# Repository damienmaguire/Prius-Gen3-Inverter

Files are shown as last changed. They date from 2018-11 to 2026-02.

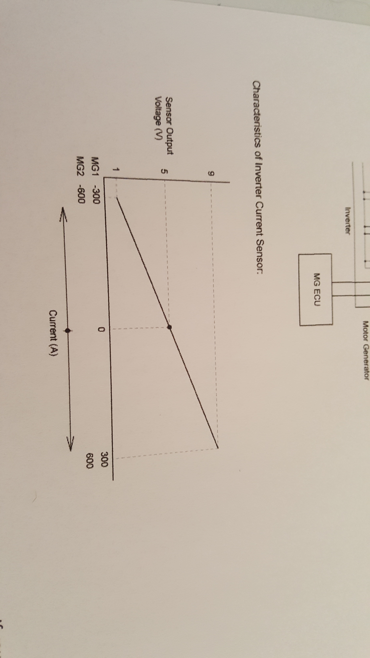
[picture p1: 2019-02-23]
current_sensor_curve.jpg

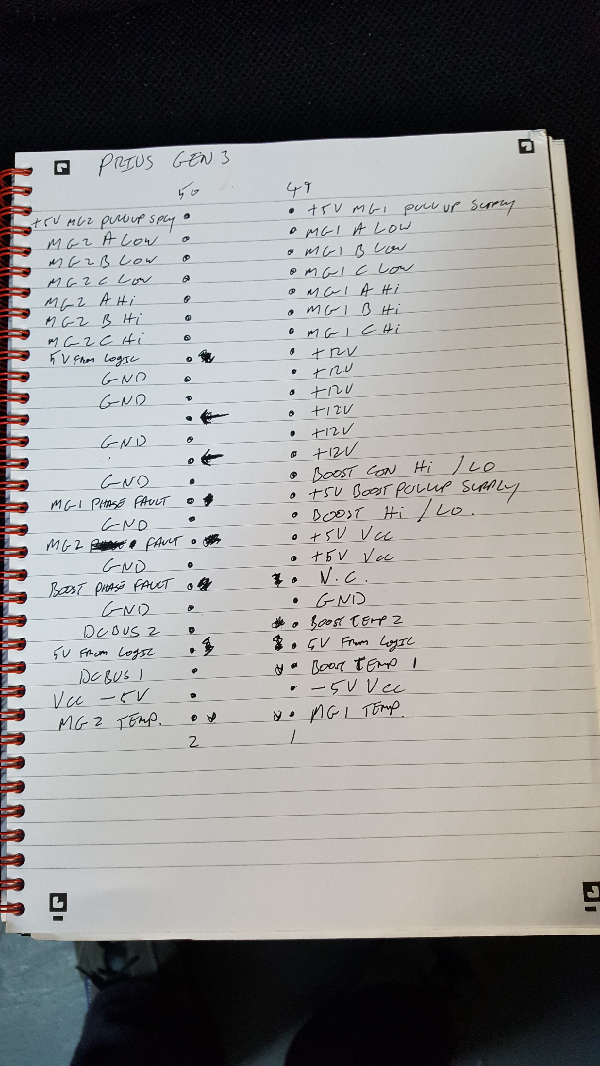
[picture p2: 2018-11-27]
IGBT_conn.jpg

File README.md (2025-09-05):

# Prius-Gen3-Inverter
Open source logic board to control the Toyota Prius Gen 3 Inverter

PCB Files in DesignSpark PCB 8.1 Format

Based on the Open Source Inverter system designed by Johannes Heubner.

27/11/18 Reverse engineering of the inverter continues. Now have all but two of the fifty pins of the igbt interface connector worked out.

01/12/18 Uploaded design for a simple breakout pcb to allow easier access to the 50 Way JST header used for connecting to the IGBT driver board.

01/03/19 Uploaded PDF of V1 logic board design for Gen 3 inverter / converter. Design on PCB commenced. Full design to be released soon.

06/03/19 : Initial release of V1 logic board design files and Gerbers. Changes likely before prototype ordering. BOM on the way.

12/03/19 : Released final design files. Now gone for pcb prototype build. Standby for fun:)

20/01/20 : Design files released for V2 board. Uses MG2 as inverter and MG1 and boost converter for battery charging. Based on the openinverter system. PCB files in DesignSpark PCB 9 format.

16/05/20 : Design files for new V1c board released.
<br>
Instalation video manual part one :
<br>
https://youtu.be/QE-zym8iIgM
<br>
Available on the webshop here :
<br>
https://www.evbmw.com/index.php/evbmw-webshop/toyota-built-and-tested-boards

28/06/20 : Road testing : https://youtu.be/Bs4mdTkqKXk

15/09/20 : New V1d Dual Motor version gerbers and schematics uploaded. This version features two STM32 MCUs to allow Both MG1 and MG2 in a Toyota hybrid transmission to be each controlled together or independently. Untested as of this date. Sources will be released in the future.

14/10/20 : Block 3 versions of V1c and V1d boards added. Changes :

V1c - Updated obsolete SG3204 charge pump -5v supply to LM2776.

V1d - Changed pullups / pulldowns on the MG1 MCU to avoid it being detected as a Tesla M3 board by the firmware.

V1d - Updated obsolete SG3204 charge pump -5v supply to LM2776.

Dual motor board working :

https://www.youtube.com/watch?v=aW6XFF3Rs8Q

18/01/2021 :(180Jacob) Small board layout of V1d uploaded. Note at time of writing, the low side output drivers are out of stock at JLC so I will change the BOM once an alternative is chosen.

05/09/25 : Added Ampseal adapter board gerber files

20/01/21 : Added Sync serial data captures between new VCU and bench rig (ct200h) and various prius and yaris bare logic boards.

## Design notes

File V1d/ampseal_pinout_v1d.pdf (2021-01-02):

## PRIUS GEN 3 V1d LOGIC BOARD AMPSEAL 35 PINOUT

PIN | FUNCTION
1 | 12V SUPPLY POSITIVE
2 | GROUND
3 | FORWARD DIRECTION SIGNAL
4 | REVERSE DIRECTION SIGNAL
5 | START SIGNAL
6 | BRAKE DIGITAL SIGNAL
7 | CRUISE CONTROL SIGNAL
8 | +5V OUT
9 | ACCELERATOR CHAN 1 INPUT
10 | ACCELERATOR CHAN 2 INPUT
11 | GROUND
12 | MG1 RESOLVER EXC
13 | MG1 STATOR TEMP SENSOR B
14 | +5V OUT
15 | MG2 ENCODER CHAN A
16 | MG2 ENCODER CHAN B
17 | GROUND
18 | RESOLVER SIN
19 | RESOLVER COS
20 | MG2 RESOLVER EXC
21 | GROUND
22 | MG2 STATOR TEMP SENSOR A

23 | MG2 STATOR TEMP SENSOR B
24 | MAIN HV CONTACTOR
25 | HV PRECHARGE RELAY
26 | CHARGER AC INPUT RELAY
27 | CHARGER HV DC REQUEST
28 | CHARGER AC PRECHARGE RELAY
29 | MG1 STATOR TEMP A
30 | EVSE PROXIMITY SIGNAL
31 | EVSE CONTROL PILOT SIGNAL
32 | CHARGER CAN HIGH
33 | CHARGER CAN LOW
34 | MG1 ENCODER CHAN A
35 | MG1 ENCODER CHAN B

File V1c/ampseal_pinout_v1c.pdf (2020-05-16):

## PRIUS GEN 3 V1c LOGIC BOARD AMPSEAL 35 PINOUT

PIN | FUNCTION
1 | 12V SUPPLY POSITIVE
2 | GROUND
3 | FORWARD DIRECTION SIGNAL
4 | REVERSE DIRECTION SIGNAL
5 | START SIGNAL
6 | BRAKE DIGITAL SIGNAL
7 | CRUISE CONTROL SIGNAL
8 | +5V OUT
9 | ACCELERATOR CHAN 1 INPUT
10 | ACCELERATOR CHAN 2 INPUT
11 | GROUND
12 | INVERTER CAN HIGH
13 | INVERTER CAN LOW
14 | +5V OUT
15 | ENCODER CHAN A
16 | ENCODER CHAN B
17 | GROUND
18 | RESOLVER SIN
19 | RESOLVER COS
20 | RESOLVER EXC
21 | GROUND
22 | MOTOR TEMP SENSOR A

23 | MOTOR TEMP SENSOR B
24 | MAIN HV CONTACTOR
25 | HV PRECHARGE RELAY
26 | CHARGER AC INPUT RELAY
27 | CHARGER HV DC REQUEST
28 | CHARGER AC PRECHARGE RELAY
29 | GROUND
30 | EVSE PROXIMITY SIGNAL
31 | EVSE CONTROL PILOT SIGNAL
32 | CHARGER CAN HIGH
33 | CHARGER CAN LOW
34 | NOT USED
35 | NOT USED

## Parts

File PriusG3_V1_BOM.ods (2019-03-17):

TOYOTA PRIUS GEN 3 INVERTER LOGIC BOARD V1 BOM
Ref Name | Qty | Component | Value | Manufacturer | MPN | RS Part Number | Mouser Part Number | Description
CONN1 | 1 | G3_Main_Conn |  | Tyco |  | See Notes(1) | See Notes(1) | Not available. Must be harvested from OEM logic PCB.
CONN8,9 | 2 | 2PinJSTCPT |  | JST (JAPAN SOLDERLESS TERMINALS) | SM02B-CPTK-1A-TB | 123-8260 |  | Wire-To-Board Connector, 2 mm, 2 Contacts, Header, CPT Series, Crimp, 1 Rows
CONN7,12,13,14,15,16 | 6 | 2SIL |  | AMPHENOL FCI | 77311-401-36LF | 771-0189 |  | Board-To-Board Connector, 2.54 mm, 36 Contacts, Header, BergStik 77311 Series, Through Hole, 1 Rows
CONN11 | 1 | 6DSIL |  | Wurth Elektronik | 61300421121 | 828-1513 |  | 2.54mm Pitch, 4 Way, 2 Row, Straight Pin Header, Through Hole
CONN3 | 1 | 8PinJSTCPT |  | JST (JAPAN SOLDERLESS TERMINALS) | SM08B-CPTK-1A-TBL |  | 306-SM08B-CPTK-1ATBL | Automotive Connectors SIDE ENTRY CPT HDR 2.0MM PITCH
C44 | 1 | 25PX680MEFC10X12.5 | 680uF | Rubycon | 25PX680MEFC10X12.5 | 711-1141 |  | RUBYCON - 25PX680MEFC10X12.5 - CAP, 680F, 25V, 20%
C104,109 | 2 | 25ZLG47MEFC6.3X7 | 47uF | Rubycon | 25ZLG47MEFC6.3X7 | 7259004 |  | Capacitor Al 105deg 47uF 25V 6.3x7 Rubycon Aluminium Electrolytic Capacitor 47uF 25 V dc 6.3mm
J2,3 | 2 | 75867-101LF |  | FCI | 75867-101LF | 6737635 |  | 2.54mm Pitch 10 Way 2 Row Shrouded Right Angle PCB Header, Through Hole
L1 | 1 | 7447709470 |  | Wurth Elektronik | 7447709470 | 789-6805 |  | SMD-Shielded Power Inductors WE-PD
IC12 | 1 | AT90S4433A | ATMEGA328P-AU | Microchip | ATMEGA328P-AU | 131-0271 |  | MICROCONTROLLER4 Kbytes FLASH128 bytes SRAM256 bytes EEPROMUART6-channel 10 bit ADC
CONN4,5 | 2 | BM08B-CPTK-1A-TB |  | JST (JAPAN SOLDERLESS TERMINALS) | BM08B-CPTK-1A-TB | 1238259 |  | Header Top 8 Double CPT
CONN2 | 1 | BM50B-SHLDS-G-TFT |  | JST (JAPAN SOLDERLESS TERMINALS) | BM50B-SHLDS-G-TFT | See Notes(2) | See Notes(2) | Top Entry disconnectable, crimp style Shrouded Header, 50 positions
C41,23,24,106,43,65,71,107,72,84,97,98,99,100,111,113,114,9,52,58 | 20 | C-USC0805 | 0.1uF | MURATA | GRM219R71C104KA01D |  | 81-GRM40X104K16D | Murata 0805 GRM 100nF Ceramic Multilayer Capacitor, 16 V dc X7R Dielectric ±10% SMD
C18,19,20,33,34,69,70,85,86,89 | 10 | C-USC0805 | 1nF | MULTICOMP | MCSH21B102K160CT | 1856432 |  | SMD Multilayer Ceramic Capacitor, 0805 [2012 Metric], 1000 pF, 16 V, ± 10%, X7R, MCSH Series
C21,22,25,26,28,29,30,31,32,45,40,77,82,83,90,91,92,93,94,95,96,101,102,112,115,6,7,14,15,53,62,11,16,64,66 | 35 | C-USC0805 | 1uF | KEMET | C0805C105K4RACTU | 9227792 |  | Kemet 0805 1μF Ceramic Multilayer Capacitor, 16V dc X7R Dielectric ±10% SMD
C46,55,56 | 3 | C-USC0805 | 10nF | Wurth Elektronik | 885012207039 | 181-4070 |  | SMD Multilayer Ceramic Capacitor, 0805 [2012 Metric], 0.01 µF, 16 V, ± 10%, X7R,
C36,37,38,49,50,73,74,75,80,81 | 10 | C-USC0805 | 22n | Avx | 08051C223KAT2A | 136-4708 |  | 22nF Multilayer Ceramic Capacitor MLCC
C1,2,4,8 | 4 | C-USC0805 | 27pF | MULTICOMP | MC0805N270J500CT | 1759196 |  | SMD Multilayer Ceramic Capacitor, 0805 [2012 Metric], 27 pF, 50 V, ± 5%, C0G / NP0, MC Series
C105,108 | 2 | C-USC0805 | 47nF | YAGEO (PHYCOMP) | CC0805KRX7R9BB473 | 718683 |  | SMD Multilayer Ceramic Capacitor, 0805 [2012 Metric], 0.047 µF, 50 V, ± 10%, X7R, CC Series
C39,76 | 2 | C-USC0805 | 330n | Avx | 08055C334KAT2A | 144-1441 |  | 330nF Multilayer Ceramic Capacitor MLCC 50V dc
C3,27,35,68,87,88,47,48,78,79 | 10 | Cap_el | 100uF | Nichicon | UPS1E101MED | 519-4059 |  | 100μF 25V dc Aluminium Electrolytic Capacitor, Through Hole 6.3 (Dia.) x 11mm +105°C 6.3mm 2.5mm
IC5 | 1 | CD74HC30M |  | Texas Instruments | CD74HC30M | 526824 |  | CD74HC30M, Logic Gate 8 Input NAND, HC, 5.2mA 2 to 6V 14-Pin SOIC
L4,5 | 2 | CLF7045T-150M |  | TDK | CLF7045T-150M | 7923997P |  | TDK CLF7045T Series Shielded Wire-wound SMD Inductor with a Ferrite Core, 15 uH +/-20% 2.3A Idc
X2,4 | 2 | CRYSTALTC26HM | 32.768kHz | RALTRON | R26-32.768- 12.5 | 1652573 |  | Crystal, 32.768 kHz, Cylinder Radial, 6.2mm x 2mm Dia, 12.5 pF, 20 ppm, R26 Series
C12,13,59,63 | 4 | C_0805 | 10pF | Wurth Elektronik | 885012007010 |  | 710-885012007010 | SMD Multilayer Ceramic Capacitor, 0805 [2012 Metric], 10 pF, 16 V, ± 5%, C0G / NP0
C5,17,60,61,10,67 | 6 | C_0805 | 10uF | MURATA | GRM21BR61E106KA73L | 790-0673 |  | SMD Multilayer Ceramic Capacitor, 0805 [2012 Metric], 10 µF, 25 V, ± 10%, X5R, GRM Series
LD1,2 | 2 | LD1117SOT223 | LD1117-3.3 | STMICROELECTRONICS | LD1117S33CTR | 686-9388 |  | Fixed LDO Voltage Regulator, 4.75V to 15V, 1.1V Dropout, 3.3Vout, 950mAout, SOT-223-4
LED2,1,3,4,5 | 5 | LED0805 |  | MULTICOMP | MCL-S270GC | 1581242 |  | LED, Green, SMD, 1.25mm x 1.4mm, 20 mA, 2.1 V, 570 nm
X1,3 | 2 | LFXTAL011301 | 8.00MHz | IQD | LFXTAL011301 | 4789656 |  | Crystal SMD 8.000MHz HC49S-SMD Crystal 8MHz, 30ppm, 2-Pin HC-49-4H-SMX
IC2,17 | 2 |  |  | Winslow | W30508TRC | 813-115 |  | 2.54mm Pitch Vertical 8 Way, Through Hole Turned Pin Open Frame IC Dip Socket
IC2,17 | 2 | LM386N |  | Texas Instruments | LM386N | 124-4528 |  | Audio Amplifiers Lo Vltg Audio PWR Amp
IC8 | 1 | LM2596S-5.0_NOPB |  | Texas Instruments | LM2596S-5.0/NOPB | 5333692 |  | SIMPLE SWITCHER 4.5V to 40V, 3A Low Component Count Step-Down Regulator
IC4,18 | 2 | LM2901DT |  | STMicroelectronics | LM2901DT | 7140745 |  | LM2901DT, Quad Comparator Open Collector 1.3s 12 V, 15 V, 18 V, 24 V, 28 V, 3 V, 5 V, 9 V 14-Pin SO
L2,3 | 2 | L_PM0603 | 10uH | TDK | MLZ1608M100WT |  | 810-MLZ1608M100WT000 | Surface Mount High Frequency Inductor, MLZ Series, 10 µH, 250 mA, 0603 [1608 Metric], Multilayer
IC3 | 1 | MAX889RESA+ |  | Maxim Integrated | MAX889RESA+ | 7861300P |  | Maxim MAX889RESA+, Charge Pump Inverting 200mA 0.62 MHz, -2.5 -5.5 V, 8-Pin, SOIC
D1,2,3,4 | 4 | MBRS540T3G |  | ON Semiconductor | MBRS540T3G | 1250012 |  | Diode Schottky 40V 5A SMC ON Semiconductor MBRS540T3G Schottky Diode, 5A, 40V, 2-Pin SMC
C51 | 1 | MCGPR10V227M6.3X11 | 220uF | MULTICOMP | MCGPR10V227M6.3X11 | 711-0808 |  | MULTICOMP - MCGPR10V227M6.3X11 - CAP, 220F, 10V, 20%
IC7,11 | 2 | MCP602-I_SN |  | Microchip | MCP602-I/SN | 3792588 |  | Dual lowpower op-amp,MCP602-I/SN SO8
C54,102 | 2 | MCRH35V477M10X21 | 470uF | MULTICOMP | MCRH35V477M10X21 | 711-1292 |  | MULTICOMP - MCRH35V477M10X21 - CAP, 470F, 35V, 20%
IC6,19 | 2 | MIC2171WU-TR |  | Micrel | MIC2171WU-TR | 998-MIC2171WUTR |  | Switching Voltage Regulators 2.5A 100kHz Switching Regulator
J1 | 1 | ML6 |  | HARTING | 9185067324 | 740-7105 |  | Harting SEK Series, 2.54mm Pitch 6 Way 2 Row Straight PCB Header
TR1,2,3,4,5,6,7,8,9,10,11,12,13,14,15 | 15 | MMBT3904 |  | Fairchild Semiconductor | MMBT3904 | 7390303 |  | NPN 40V 0.2A SOT23 Fairchild MMBT3904 NPN Bipolar Transistor, 0.2 A, 40 V, 3-Pin SOT-23
IC13,14 | 2 | NCV8401ADTRKG |  | ON Semiconductor | NCV8401ADTRKG | 8079877 |  | ON Semiconductor NCV8401ADTRKG Load Switch IC 3-Pin, DPAK
R125,126,53 | 3 | R-US_R0805 | 0R | RS Pro | 717-1578 | 717-1578 |  | 0R 0805 Thick Film Surface Mount Fixed Resistor ±5% 0.125W
R8,6,38,39,40,41,42,43,58,89,98,99,100,101,102,103,129,130,153,154,164,165,178,179,180,181,152,182,183,184,185,186,187,188,189,190,191,192,195,196 | 40 | R-US_R0805 | 1k | MULTICOMP | MC01W080551K | 9333711 |  | SMD Chip Resistor, Thick Film, 1 kohm, 150 V, 0805 [2012 Metric], 100 mW, ± 5%, MC Series
R52,166,174,176 | 4 | R-US_R0805 | 1K2 | RS Pro | 713-6941 | 713-6941 |  | 1.2kΩ 0805 Thick Film Surface Mount Fixed Resistor ±5% 0.125W
R24,26,28,32,33,141,143,144,146,147 | 10 | R-US_R0805 | 1K5 | Panasonic | ERJ6RBD1501V | 2380317 |  | SMD Chip Resistor, Thick Film, 1.5 kohm, 150 V, 0805 [2012 Metric], 100 mW, ± 0.5%, ERJ6E Series
R57,65,118,167,173,175 | 6 | R-US_R0805 | 2K2 | RS Pro | 804-6455 | 804-6455 |  | 1.5kΩ 0805 Thick Film Surface Mount Fixed Resistor ±1% 0.125W
R3,7,17,66,67,104,105,119,120,135 | 10 | R-US_R0805 | 3K3 | Panasonic | ERJ6RBD3301V | 2380370 |  | SMD Chip Resistor, Thick Film, 3.3 kohm, 150 V, 0805 [2012 Metric], 100 mW, ± 0.5%, ERJ6E Series
R48,110 | 2 | R-US_R0805 | 3K16 | RS Pro | 717-2644 | 717-2644 |  | 3.16kΩ 0805 Thick Film Surface Mount Fixed Resistor ±1% 0.125W
R47,23,25,27,31,34,109,142,145,148,149,150,11,90 | 14 | R-US_R0805 | 4K7 | Panasonic | ERJ6RBD4701V | 2380397 |  | SMD Chip Resistor, Thick Film, 4.7 kohm, 150 V, 0805 [2012 Metric], 100 mW, ± 0.5%, ERJ6E Series
R160,162 | 2 | R-US_R0805 | 9K1 | RS Pro | 804-6512 | 804-6512 |  | 9.1kΩ 0805 Thick Film Surface Mount Fixed Resistor ±1% 0.125W
R2,4,9,10,12,14,15,46,51,1,18,19,20,21,29,30,36,37,22,55,59,60,13,91,92,93,94,95,96,108,113,114,115,122,123,124,127,128,136,137,138,139,140,151,156,168,169,,170,171,172,177 | 51 | R-US_R0805 | 10k | BOURNS | CRT0805-FZ-1002ELF | 2008317 |  | SMD Chip Resistor, Thin Film, 10 kohm, 100 V, 0805 [2012 Metric], 100 mW, ± 1%, CRT Series
R68,121 | 2 | R-US_R0805 | 10R | RS Pro | 713-6771 | 713-6771 |  | 10R 0805 Thick Film Surface Mount Fixed Resistor ±5% 0.125W
R35,73 | 2 | R-US_R0805 | 56K | RS Pro | 804-6580 | 804-6580 |  | 56kΩ 0805 Thick Film Surface Mount Fixed Resistor ±1% 0.125W
R69,70,116,117 | 4 | R-US_R0805 | 60R4 | TE CONNECTIVITY | RN73C2A60R4BTDF | 2688288RL |  | SMD Chip Resistor, Precision, 60.4 ohm, 100 V, 0805 [2012 Metric], 100 mW, ± 0.1%
R44,49,106,111 | 4 | R-US_R0805 | 62K | RS Pro | 804-6584 | 804-6584 |  | 62kΩ 0805 Thick Film Surface Mount Fixed Resistor ±1% 0.125W
R74,75,76,77,78,79,193,194,82,83,84,85,86,87 | 14 | R-US_R0805 | 91R | RS Pro | 804-6363 | 804-6363 |  | 91Ω 0805 Thick Film Surface Mount Fixed Resistor ±1% 0.125W
R45,50,107,112,157,159 | 6 | R-US_R0805 | 100K | MULTICOMP | MC01W08055100K | 9333738 |  | SMD Chip Resistor, 100 kohm, 150 V, 0805 [2012 Metric], 100 mW, ± 5%, MC Series
R61,62,63,64,131,132,133,134 | 8 | R-US_R0805 | 220R | RS Pro | 713-6884 | 713-6884 |  | 220Ω 0805 Thick Film Surface Mount Fixed Resistor ±5% 0.125W
R158 | 1 | R-US_R0805 | 300K | RS Pro | 804-6644 | 804-6644 |  | 300kΩ 0805 Thick Film Surface Mount Fixed Resistor ±1% 0.125W
R5,88,155,163 | 4 | R-US_R0805 | 470R | RS Pro | 804-6417 | 804-6417 |  | 470Ω 0805 Thick Film Surface Mount Fixed Resistor ±1% 0.125W
R56,71,72 | 3 | R-US_R0805 | 560R | VISHAY | CRCW0805560RFKEA | 1469945 |  | SMD Chip Resistor, Thick Film, 560 ohm, 150 V, 0805 [2012 Metric], 125 mW, ± 1%
R161 | 1 | R-US_R0805 | 820R | RS Pro | 713-6932 | 713-6932 |  | 820Ω 0805 Thick Film Surface Mount Fixed Resistor ±5% 0.125W
X5 | 1 | RESONATORMU | 16MHz | MURATA | CSTCE16M0V53A-R0 | 721-4818 |  | Ceramic Resonator, 16MHz Fundamental 15pF, 3-Pin Cap Chip
IC9,16 | 2 | SN65HVD234 | SN65HVD234 | TEXAS INSTRUMENTS | SN65HVD234D | 1212363 |  | CAN Bus, Transceiver, CAN, 1, 1, 3 V, 3.6 V, SOIC
IC1,10 | 2 | STM32F103 | STM32F103RBT6 | STMICROELECTRONICS | STM32F103RBT6 | 1447640 |  | ARM Microcontroller, Motor Control, ARM Cortex-M3, 32bit, 72 MHz, 128 KB, 20 KB, 64 Pins
CONN6,10 | 2 | T821120A1S100CEU |  | AMPHENOL | T821120A1S100CEU | 8323499 |  | 2.54mm Pitch 20 Way 2 Row Shrouded Straight PCB Header, Through Hole, Solder Termination
IC20 | 1 | ULN2003ADR |  | Texas Instruments | ULN2003ADR | 6658699P |  | Texas Instruments ULN2003ADR, 7-element NPN Darlington Transistor Array, 0.5 A 50 V, 16-Pin SOIC
BOM Notes : 1) Conn 1 is a Tyco part but on their restricted list so must be removed from OEM board. (2) Conn 2 only available from ChipOneStop In Japan : https://www.chip1stop.com/USA/en/product/detail?mpn=BM50B-SHLDS-G-TFT%28LF%29%28SN%29&partId=JST1-0008157 (3) IC2,IC17 to be socketed.

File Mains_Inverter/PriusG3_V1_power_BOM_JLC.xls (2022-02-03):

Comment | Designator | Package | LCSC Part #
1N4148WS | D1,D4,D3,D7 | SOD-323F | C2128
ATMEGA328P-AU | IC10 | TQFP-32_7.0x7.0x0.8P | C14877
0.1uF | C18,C6,C24,C31,C30,C38,C5,C11,C9,C10,C21 | 0805_C | C49678
1nF | C37,C34,C35,C36,C26,C25 | 0805_C | C46653
1uF | C28,C1,C2,C13 | 0805_C | C28323
10nF | C23,C3,C27 | 0805_C | C1710
4.7uF | C33,C29,C32 | 1206_C | C29823
1.5NF | C7 | 0805_C | C1717
10uF | C22,C20 | 0805_C | C15850
DB107S | BR1,BR2,BR3 | DBS | C5377
RED LED | LED1,LED2 | LED_0805 | C84256
MC34063ABD-TR | IC5 | SOP-8_3.9x4.9x1.27P | C81155
MCP2515-I/SO | IC9 | SOIC-18_7.5x11.5x1.27P | C12368
MMBT3904 | TR3,TR6,TR4,TR7,TR5,TR8,TR10,TR9,TR1,TR2,TR11 | SOT-23-3 | C20526
MP2359DJ-LF-Z | IC6 | TSOT-23-6 | C14259
MWSA0402S-3R3MT | L1 | SMD-PIND-4.2x4.4x2.0_0.8x2.0 | C408336
NCV8402ASTT1G | IC1,IC2,IC3,IC4 | SOT-223 | C77755
0Ω | R1,R33 | 0805_R | C17477
1KΩ | R31,R36,R32,R27,R75,R63,R11,R41,R44,R45,R43,R46,R74,R76,R8,R29,R30 | 0805_R | C17513
1.5KΩ | R6,R10 | 0805_R | C4310
2.2KΩ | R26 | 0805_R | C17520
2.4KΩ | R28 | 0805_R | C17526
2.7KΩ | R5 | 0805_R | C17530
3.3KΩ | R61,R68 | 0805_R | C17520
3.6KΩ | R48,R57 | 0805_R | C17526
4.7KΩ | R35,R34,R37,R38 | 0805_R | C17530
6.2KΩ | R47,R56 | 0805_R | C17767
8.2KΩ | R13 | 0805_R | C17828
10KΩ | R15,R17,R18,R14,R19,R12,R62,R40,R9,R69,R16,R2,R55 | 0805_R | C17414
22KΩ | R7 | 0805_R | C17560
43KΩ | R21 | 0805_R | C17695
47kΩ | R25 | 0805_R | C17713
0.22Ω | R23 | 0805_R | C36234
100KΩ | R60,R58,R24 | 0805_R | C17407
100Ω | R67,R66,R49,R52,R50,R53,R51,R54,R64,R71,R65,R72,R70,R73 | 0805_R | C17408
120Ω | R20 | 0805_R | C17437
180Ω | R22 | 0805_R | C25270
300KΩ | R59 | 0805_R | C17616
330Ω | R3 | 0805_R | C17630
560Ω | R39 | 0805_R | C28636
680Ω | R4 | 0805_R | C17798
SGM3204 | PS1 | SOT-23-6L | C194031
SS54 | D2,D5,D6 | SMA,DO-214AC | C22452
220uH | L2 | SMD-PIND-12.5x12.5x5_2.9x5.4 | C169402
100uF 6.3V | C12,C14,C16,C19,C17 | CASE-B_3528 | C16133
TJA1050T | IC7 | SOIC-8_3.9x4.9x1.27P | C6952
100uf 25v | C4 | SMD-ECAP-6.3x7.7 | C176675
470uF 25V | C8 | SMD-ECAP-10x10 | C249931
330uF 35V | C15 | SMD-ECAP-10x10 | C134522
16MHZ | X1,X2,X3 | SMD-3225_4P | C13738
3V3 REG | LD1 | SOT-23-3L | C5446

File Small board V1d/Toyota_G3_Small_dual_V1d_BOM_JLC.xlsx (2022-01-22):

Comment | Designator | Footprint | JLCPCB Part #
1N4148WS | D1,D4,D3,D8,D7 | SOD-123 | C81598
AMS1117-3.3 | IC15 | SOT-223 | C6186
ATMEGA328P-AU | IC14 | TQFP-32_7.0x7.0x0.8P | C14877
0.1uF | C44,C54,C64,C88,C89,C65,C55,C13,C28,C51,C73 | 0805_C | C49678
1nF | C87,C67,C68,C33,C32,C69,C84,C85,C47,C46 | 0805_C | C46653
1uF | C12,C14,C6,C8,C10,C5,C9,C11,C4,C56,C1,C2,C90,C21,C31,C59,C53,C62,C60,C25,C71,C72,C76,C77,C83,C82,C61 | 0805_C | C28323
10nF | C50,C57,C48,C70 | 0805_C | C1710
22n | C43,C39,C35,C29,C23,C24,C74,C75,C78,C79,C80,C36 | 0805_C | C1729
22pF | C49,C45,C17,C16 | 0805_C | C1804
2.2uF | C91,C66 | 0805_C | C49217
1n5 | C15 | 0805_C | C1717
10uF | C41,C52,C20,C3,C18,C81,C58,C86,C92 | 0805_C | C15850
RED LED | LED1,LED2,LED4 | LED_0805 | C84256
10uH | L1,L4 | 0603 | C1035
MH2029-300Y | L5,L6 | 0805 | C1046
MC34063ABD-TR | IC7 | SOP-8_3.9x4.9x1.27P | C81155
MCP2515-I/SO | IC12 | SOIC-18_7.5x11.5x1.27P | C12368
MMBT3904 | TR1,TR4,TR2,TR5,TR3,TR6,TR15,TR14,Q1,TR7,TR8,TR11,TR9,TR12,TR10,TR13 | SOT-23-3 | C20526
NCV8402ASTT1G | IC3,IC1,IC6,IC4,IC2 | SOT-223 | C77755
0Ω | R64,R1,R135,R137,R59,R82 | 0805_R | C17477
1KΩ | R63,R61,R67,R78,R99,R77,R98,R60,R44,R43,R117,R104,R22,R28,R9,R25,R70,R73,R71,R72,R74,R116,R118,R47,R8,R111,R51,R54,R52,R55,R53,R56,R129,R130,R131,R132,R133,R127,R134,R83,R84,R119 | 0805_R | C17513
1.2KΩ | R114,R138 | 0805_R | C17379
1.5KΩ | R14,R16,R20,R11,R18,R6 | 0805_R | C4310
2.2KΩ | R115,R136,R139 | 0805_R | C17520
2.4KΩ | R39 | 0805_R | C17526
2.7KΩ | R5 | 0805_R | C17530
3.3KΩ | R57,R50,R96,R108,R120,R122 | 0805_R | C26010
3.6KΩ | R92,R80,R45,R46 | 0805_R | C18359
4.7KΩ | R17,R12,R19,R15,R21,R68,R121 | 0805_R | C17673
6.2KΩ | R79,R91,R42,R41 | 0805_R | C17767
8.2KΩ | R140,R141 | 0805_R
10KΩ | R75,R58,R76,R49,R48,R24,R27,R23,R26,R97,R69,R10,R109,R2,R13,R124,R125,R126,R40 | 0805_R | C17414
10Ω | R37,R123 | 0805_R | C17734
22KΩ | R7,R142 | 0805_R | C17560
47kΩ | R38 | 0805_R | C17713
0.22Ω | R36 | 0805_R | C36234
100KΩ | R95,R93,R143 | 0805_R | C17407
100Ω | R107,R106,R81,R87,R85,R88,R86,R89,R101,R100,R105,R112,R110,R113 | 0805_R | C17408
120Ω | R31 | 0805_R | C17437
180Ω | R35 | 0805_R | C25270
220Ω | R29,R30,R33,R34 | 0805_R | C17557
300KΩ | R94 | 0805_R | C17616
330Ω | R3 | 0805_R | C17630
560Ω | R66 | 0805_R | C28636
680Ω | R62,R4,R128 | 0805_R | C17798
LM2776DBVR | IC17 | SOT-23-6L | C69527
SN74LVC1G00DCKR | IC16 | SOT-353 | C8185
SS54 | D5,D2,D6 | SMA,DO-214AC | C22452
STM32F103RBT6 | IC13,IC9 | LQFP-64_10.0x10.0x0.5P | C8735
220uH | L3 | SMD-PIND-12.5x12.5x5_2.9x5.4 | C169391
68uH | L2 | SMD-PIND-12.5x12.5x8_2.9x5.4 | C169377
100uF 6.3V | C63,C30,C34,C38,C40,C19,C22 | CASE-B_3528 | C16133
TDA2822 | IC10 | SOP-8_3.9x4.9x1.27P | C73296
TJA1050T | IC11 | SOIC-8_3.9x4.9x1.27P | C6952
100uf 25v | C27 | SMD-ECAP-6.3x7.7 | C176664
330uF 25V | C7 | SMD-ECAP-8x10 | C134842
330uF 35V | C37 | SMD-ECAP-10x10 | C311621
8MHz | X1,X3 | SMD-5032_2P | C115962
16MHZ | X2,X4 | SMD-3225_4P | C13738
XL1509-5.0E1 | IC5 | SOP-8_3.9x4.9x1.27P | C61063
SI2301CDS-T1-GE3 | Q2 | SOT-23 | C10487

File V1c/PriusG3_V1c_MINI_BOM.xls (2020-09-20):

Comment | Designator | Package | LCSC Part # | Element14 Part # | chip1stop.com
Coolant Temp Sensor | CONN1 | SM02B-CPTK-1A-TB | C595136 | 2708677
MG2 Current Sense | CONN2 | BM08B-CPTK-1A-TB | C594390 | 2708676
DC/DC On/Off Jumper | CONN3 | 2SIL
ACS758LCB-100U output current sensor (Alegro) | CONN4 | 3WAY_SIL
DCDC Output Volt CON | CONN5 | 2SIL
IGBT Board Interface | CONN6 | BM50B-SHLDS-G-TFT | N.A. | N.A. | C1S404000081575
MG1 Current Sense | CONN7 | BM08B-CPTK-1A-TB | C594390 | 2708676
External HVIL | CONN8 | SM02B-CPTK-1A-TB | C595136 | 2708677
FTDI Header for CHG MCU | CONN9 | 6SIL
DC/DC Converter Interface | CONN10 | SM08B-CPTK-1A-TB | C264977 | 2708679
Main Input Connector 34 Way IDC to input PCB | J1 | 75869-106LF | N.A. | 1103954
ESP WiFi Module | J2 | 75867-101LF | C598980 | 1103956
ICSP Header for CHG MCU | J3 | Pin Header Strip (2 singles)
Tag Connect JTAG | J3 | TC2050-IDC-NL | N.A. | N.A
Single Wire Programming Port STM32 | SWPR001 | Pin Header Strip

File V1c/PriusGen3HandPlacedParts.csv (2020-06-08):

Ref Name | Qty | Component | Value | Manufacturer | MPN | RS Part Number | Mouser Part Number | LCSC Part Number | Description
CONN1; CONN8 | 2 | 2PinJSTCPT |  | JST | SM02B-CPTK-1A-TB | 123-8260 |  |  | Wire-To-Board Connector 2mm 2-Contacts Header CPT Series Crimp 1 Rows
CONN2; CONN7 | 2 | BM08B-CPTK-1A-TB |  | JST | BM08B-CPTK-1A-TB | 1238259 |  |  | Header Top 8 Double CPT
CONN3; CONN5 | 2 | PIN HEADER |  |  |  |  |  |  | 2X1X2.5MM Jumpers for DC/DC operation
CONN4; SWPR001 | 2 | PIN HEADER |  |  |  |  |  |  | 3x1x2.5MM
CONN6 | 1 | BM50B-SHLDS-G-TFT |  | JST | BM50B-SHLDS-G-TFT | See Notes | See Notes | See Notes | Top Entry disconnectable crimp style Shrouded Header 50 positions
CONN9 | 1 | PIN HEADER |  |  |  |  |  |  | 1X6X2.5
CONN10 | 1 | 8PinJSTCPT |  | JST | SM08B-CPTK-1A-TBL |  | 306-SM08B-CPTK-1ATBL |  | Automotive Connectors SIDE ENTRY CPT HDR 2.0MM PITCH
J1 | 1 | 90º LOCKING IDC |  | 3M | N3431-5302RB | 5429153 | 517-N3431-5302RB |  | 3M 3000 Series; 2.54mm Pitch 34 Way 2 Row Right Angle PCB Header; Solder Term; 2A
J2 | 1 | 90º PIN HEADER |  | 3M | N2510-5002RB | 5428908 | 517-N2510-5002RB |  | Header; High Temperature; PCB Plug; 10 Cont; Solder Tail; Thru-Hole; 2500 Series; 2A
J3 | 1 | ML6 |  | HARTING | 9185067324 | 740-7105 |  |  | Harting SEK Series 2.54mm Pitch 6 Way 2 Row Straight PCB Header
NOTES: CONN2 available from ChipOneStop In Japan

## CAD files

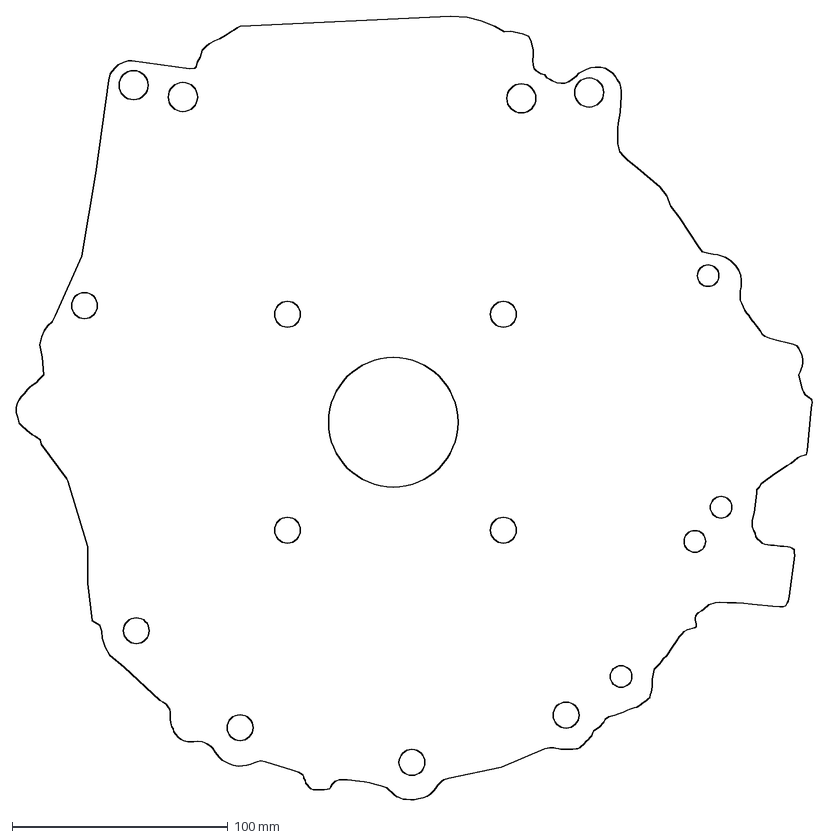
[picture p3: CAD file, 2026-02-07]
Transaxle/CAD/PriusGen3_Bell1-BodySketch.dxf
368.6 x 362.8 mm

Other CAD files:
Transaxle/CAD/PriusGen3_Bell1.FCStd

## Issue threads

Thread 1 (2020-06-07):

Part numbers for non mechanically placed parts, version V1C

DOSputin, 2020-06-07:
A BOM is included for  V1C that lists the SMT parts that are placed from the JLCPCB library.  Parts numbers, designators and descriptions for the hand placed parts are missing from this BOM.  Please include these part numbers in a separate BOM file to help others in sourcing parts for assembly of boards.

damienmaguire, 2020-10-14:
https://github.com/damienmaguire/Prius-Gen3-Inverter/blob/master/V1c/PriusGen3HandPlacedParts.csv

damienmaguire, 2021-12-01:
Closed. Hand placed bom now on repo.

Closed 2021-12-01.

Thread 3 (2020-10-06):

SGM3204 Discontinued

SRFirefox, 2020-10-06:
The SGM3204 part is unavailable from JLC and a check with LCSC indicates it is no longer in production. Depending on output current requirements, the OnSemi MAX1720 might make a drop-in replacement. If more current is required, the TI LM2776 is rated to 200mA, but has a different pinout than the original IC.

damienmaguire, 2020-10-14:
Updated designs. Thanks for the heads up.

damienmaguire, 2021-12-01:
Updated in Block 4 release to MAX735

Closed 2021-12-01.

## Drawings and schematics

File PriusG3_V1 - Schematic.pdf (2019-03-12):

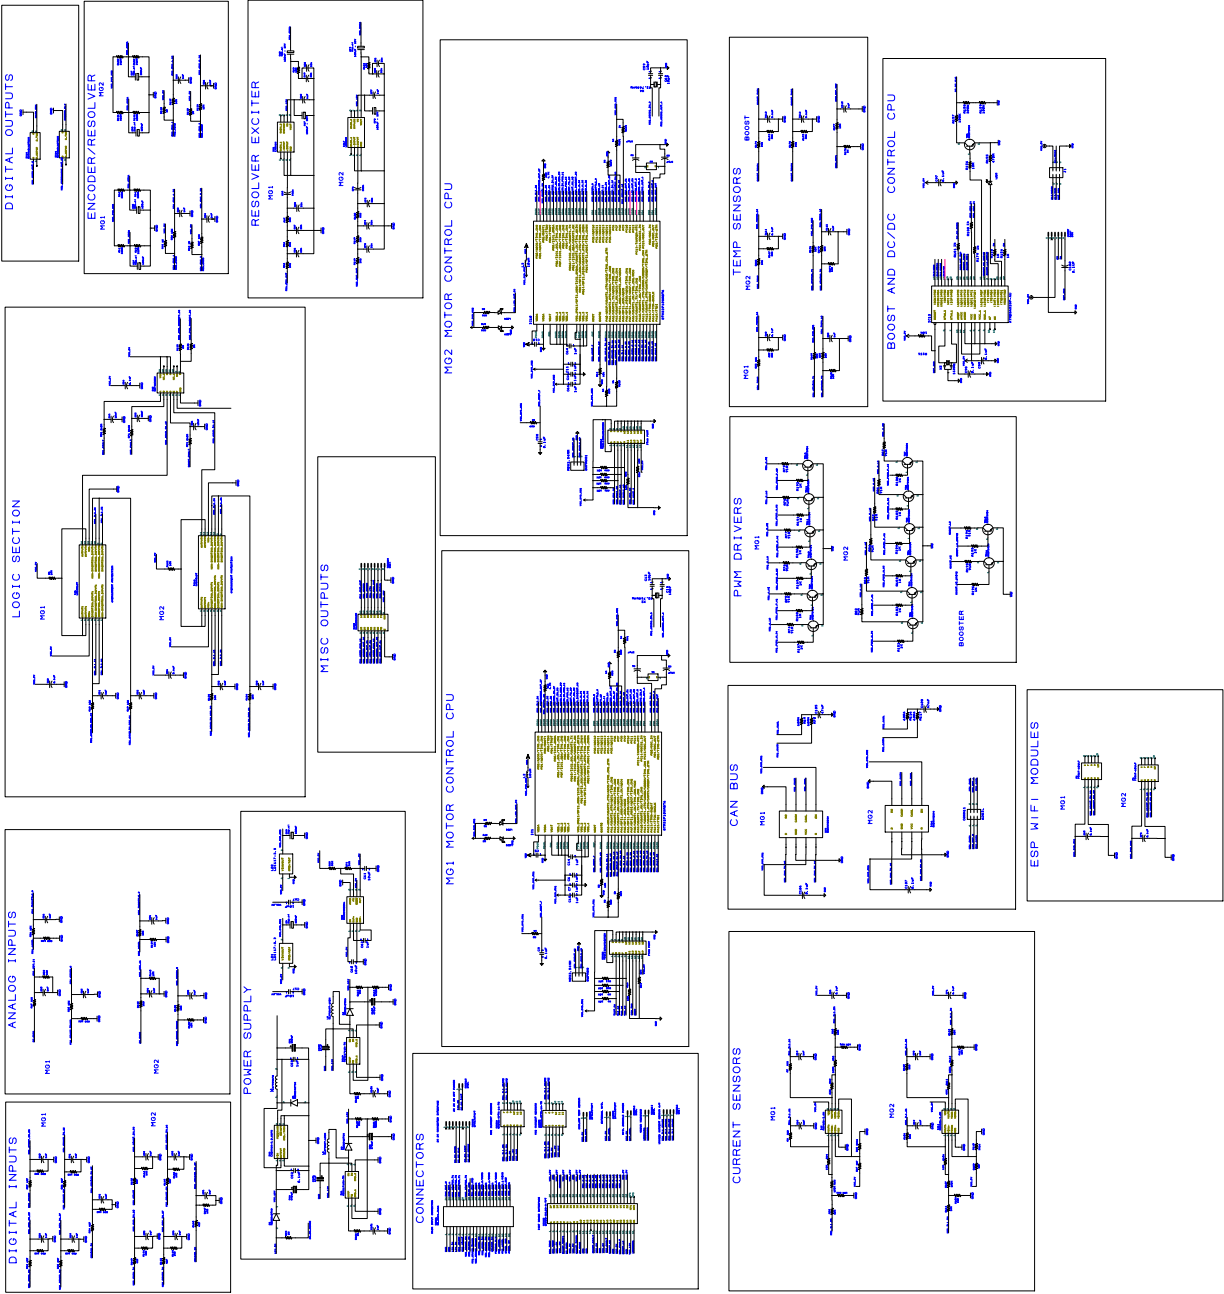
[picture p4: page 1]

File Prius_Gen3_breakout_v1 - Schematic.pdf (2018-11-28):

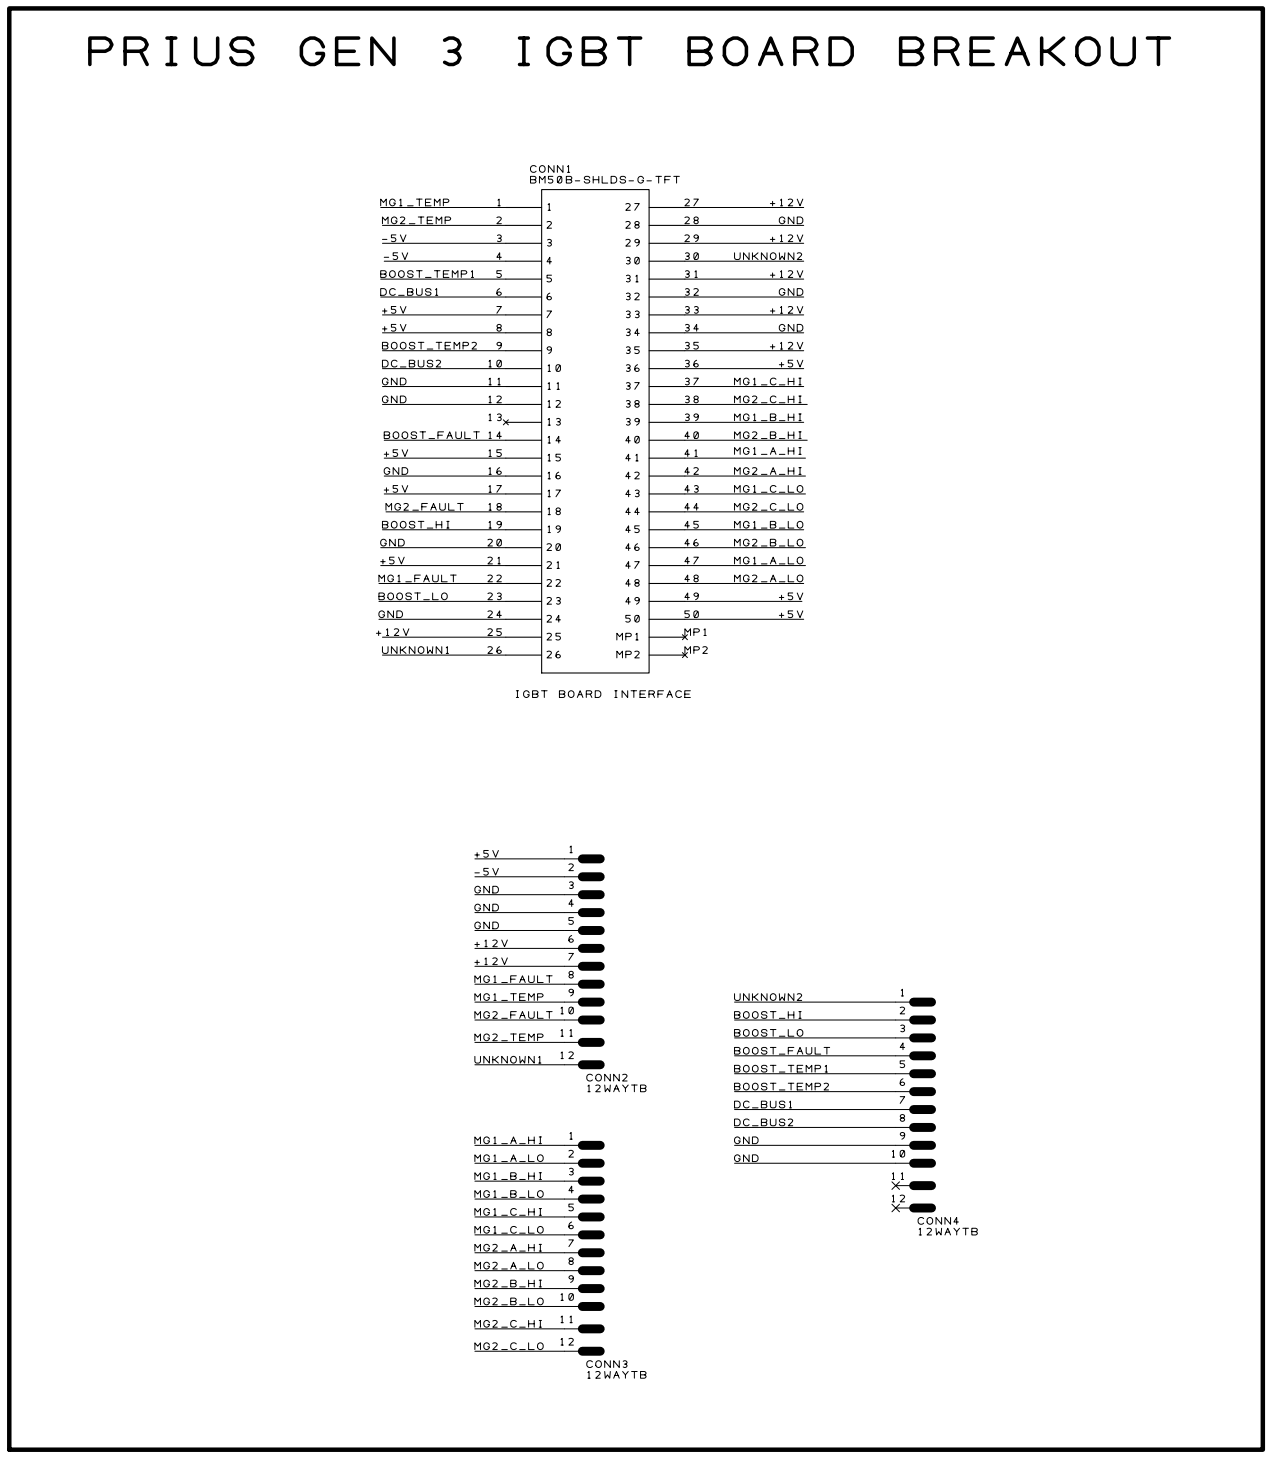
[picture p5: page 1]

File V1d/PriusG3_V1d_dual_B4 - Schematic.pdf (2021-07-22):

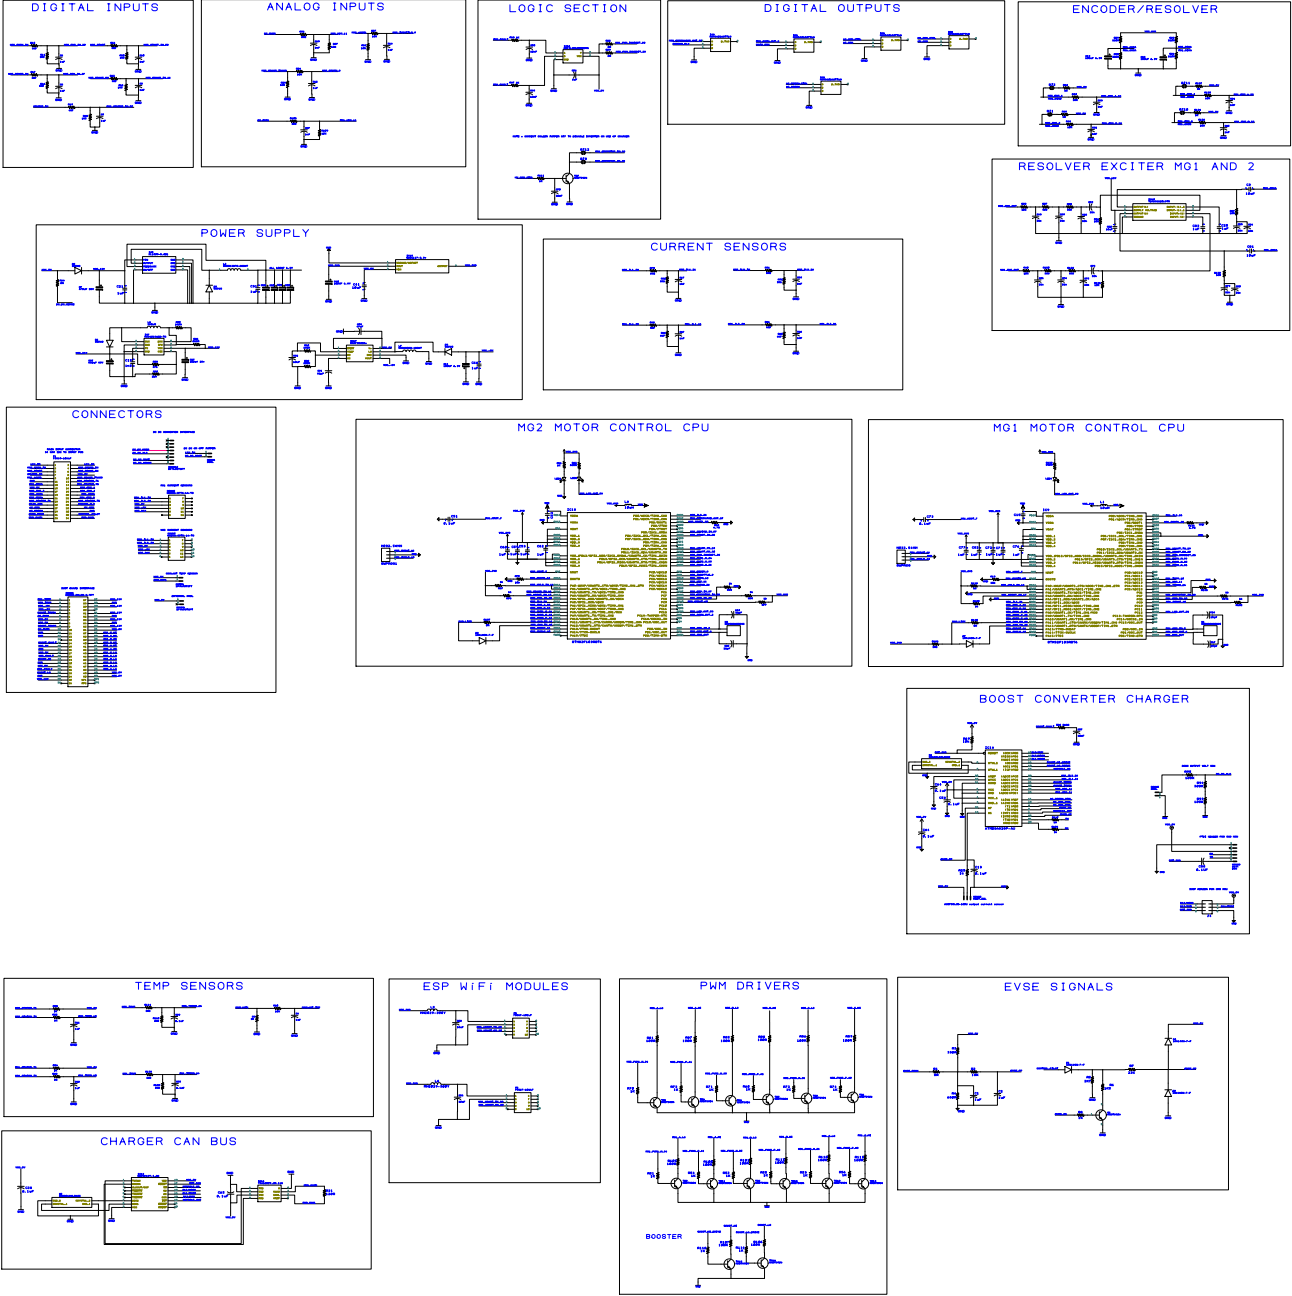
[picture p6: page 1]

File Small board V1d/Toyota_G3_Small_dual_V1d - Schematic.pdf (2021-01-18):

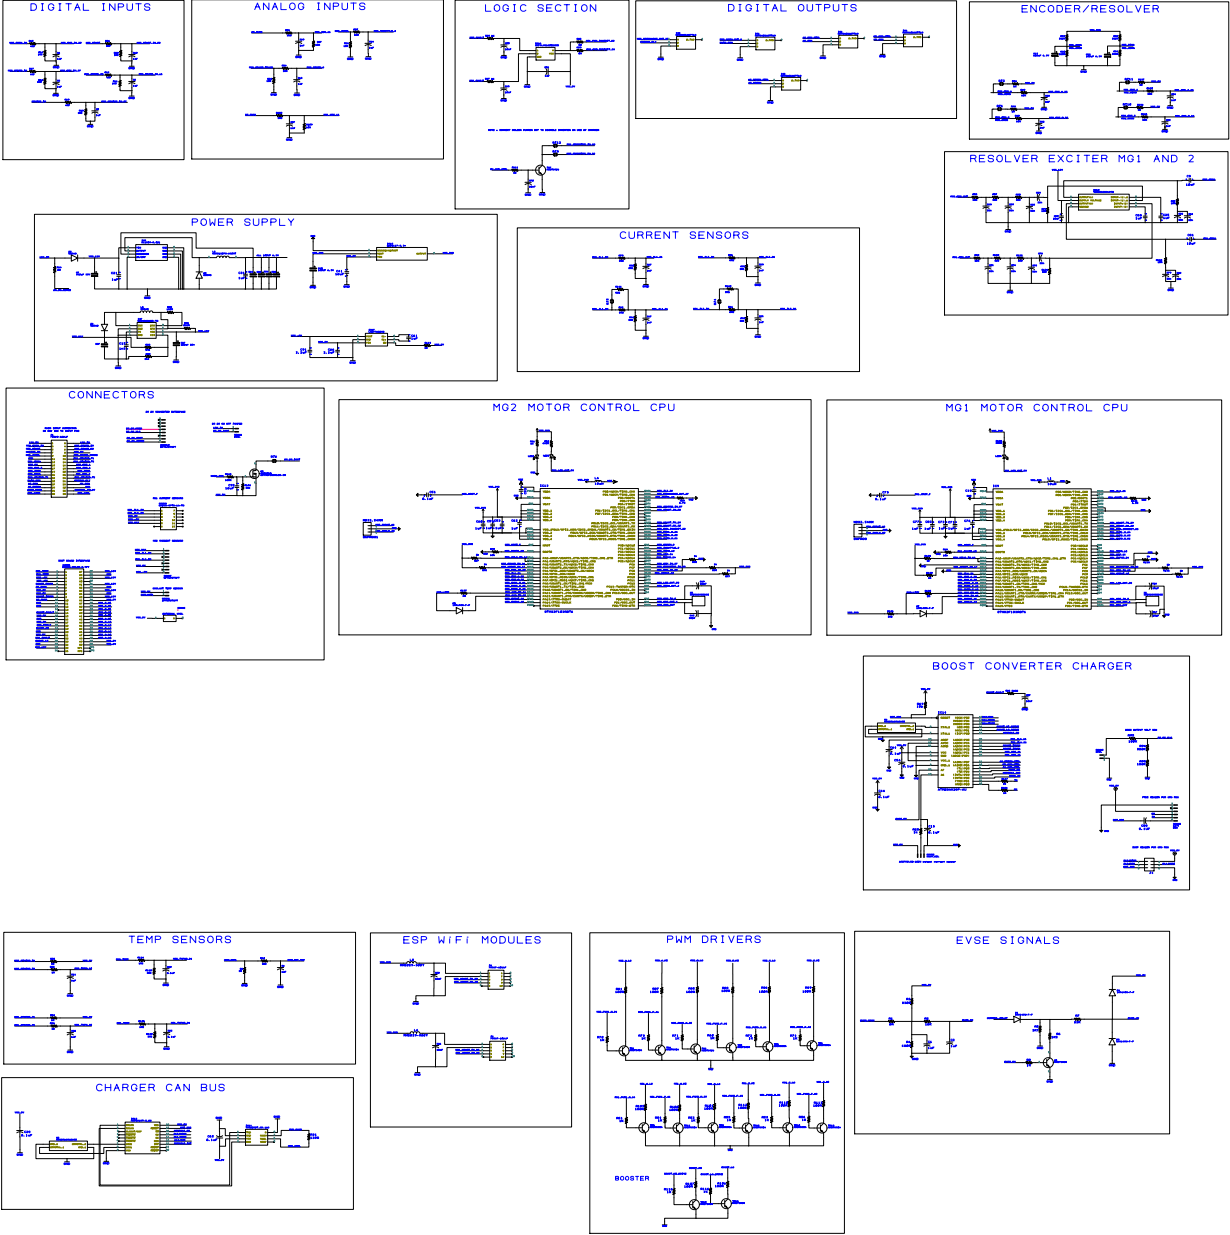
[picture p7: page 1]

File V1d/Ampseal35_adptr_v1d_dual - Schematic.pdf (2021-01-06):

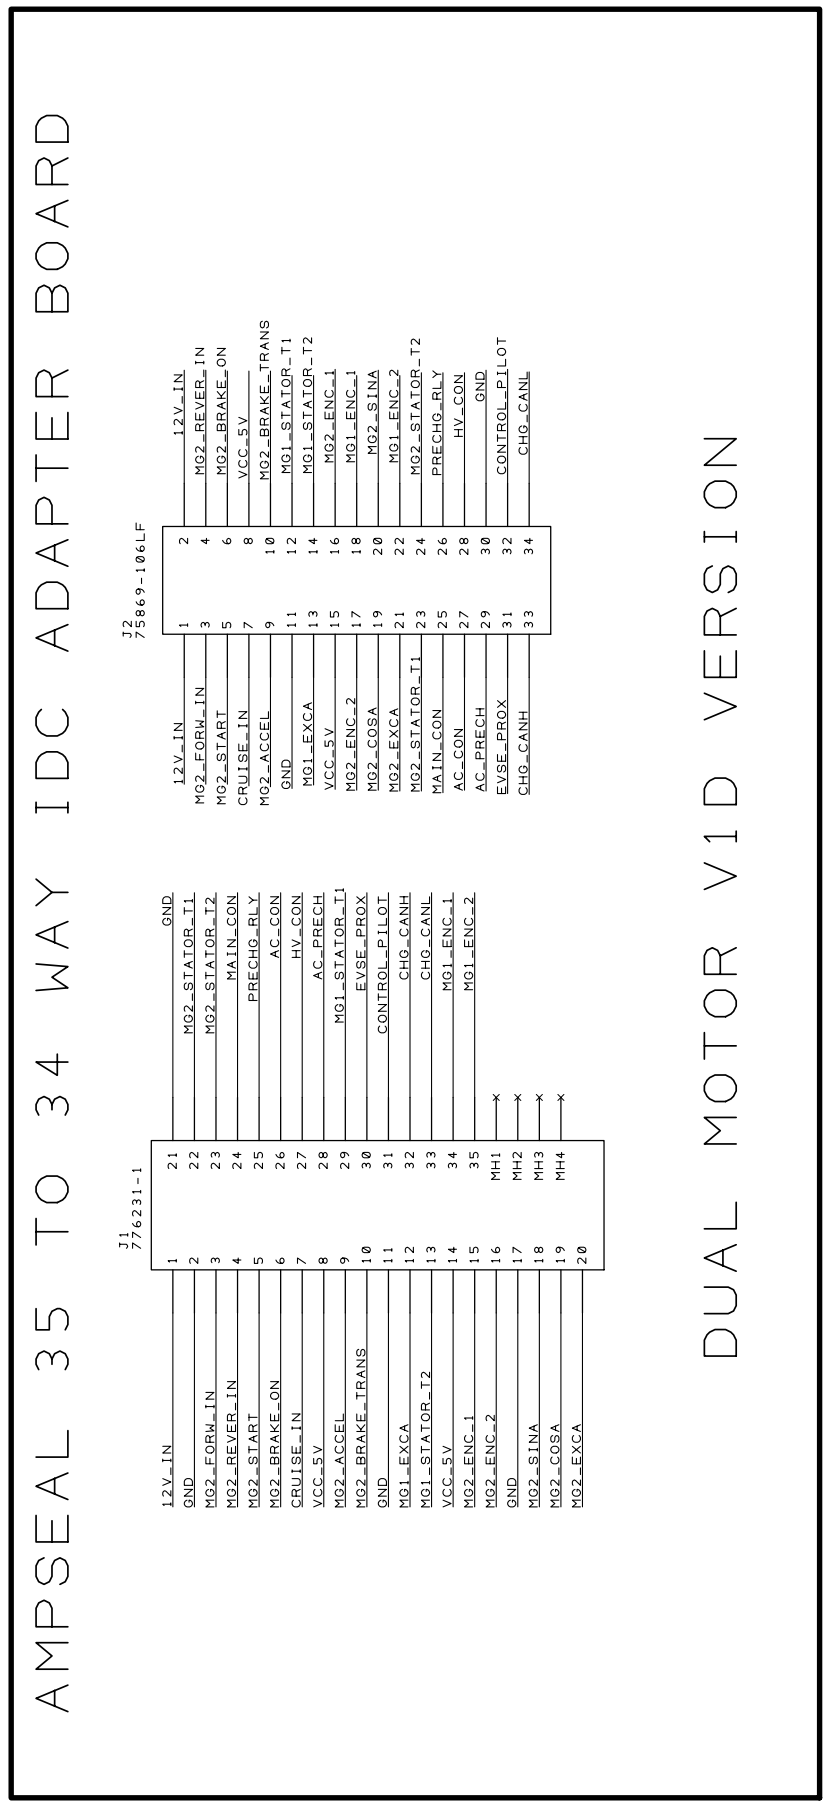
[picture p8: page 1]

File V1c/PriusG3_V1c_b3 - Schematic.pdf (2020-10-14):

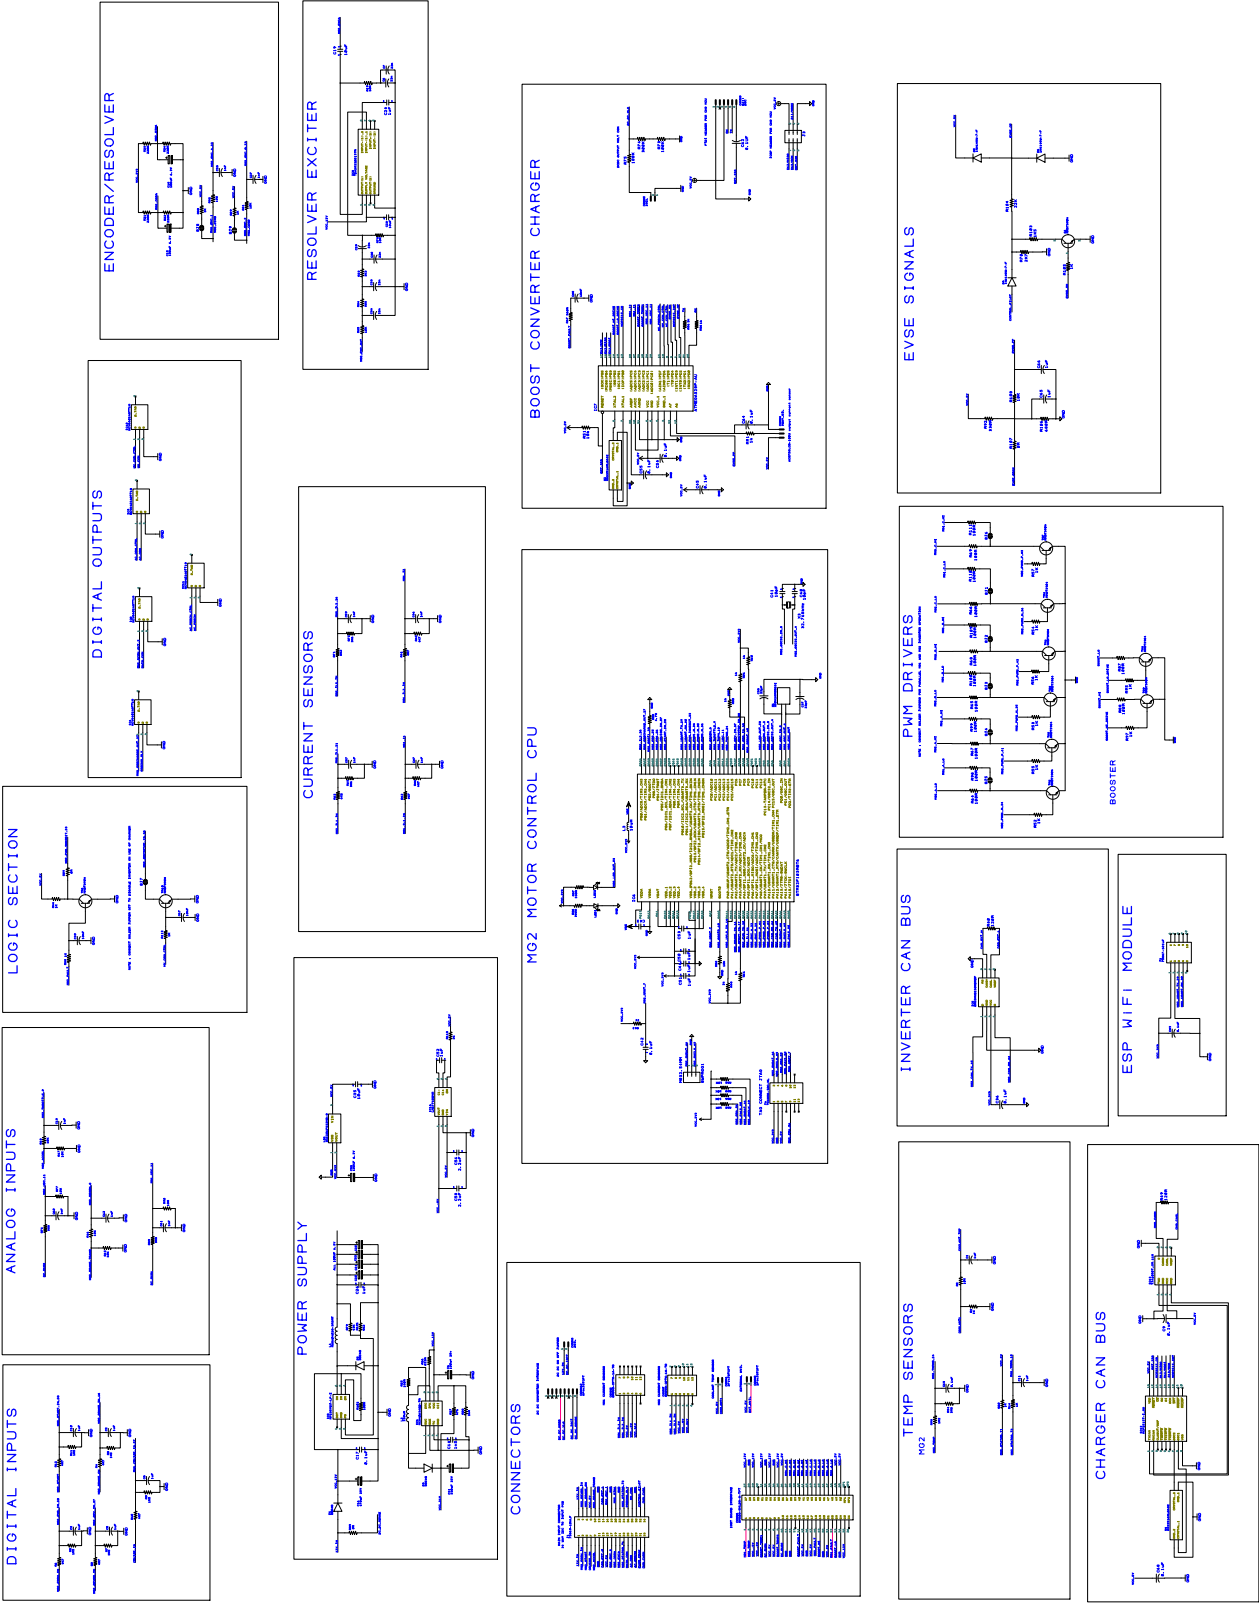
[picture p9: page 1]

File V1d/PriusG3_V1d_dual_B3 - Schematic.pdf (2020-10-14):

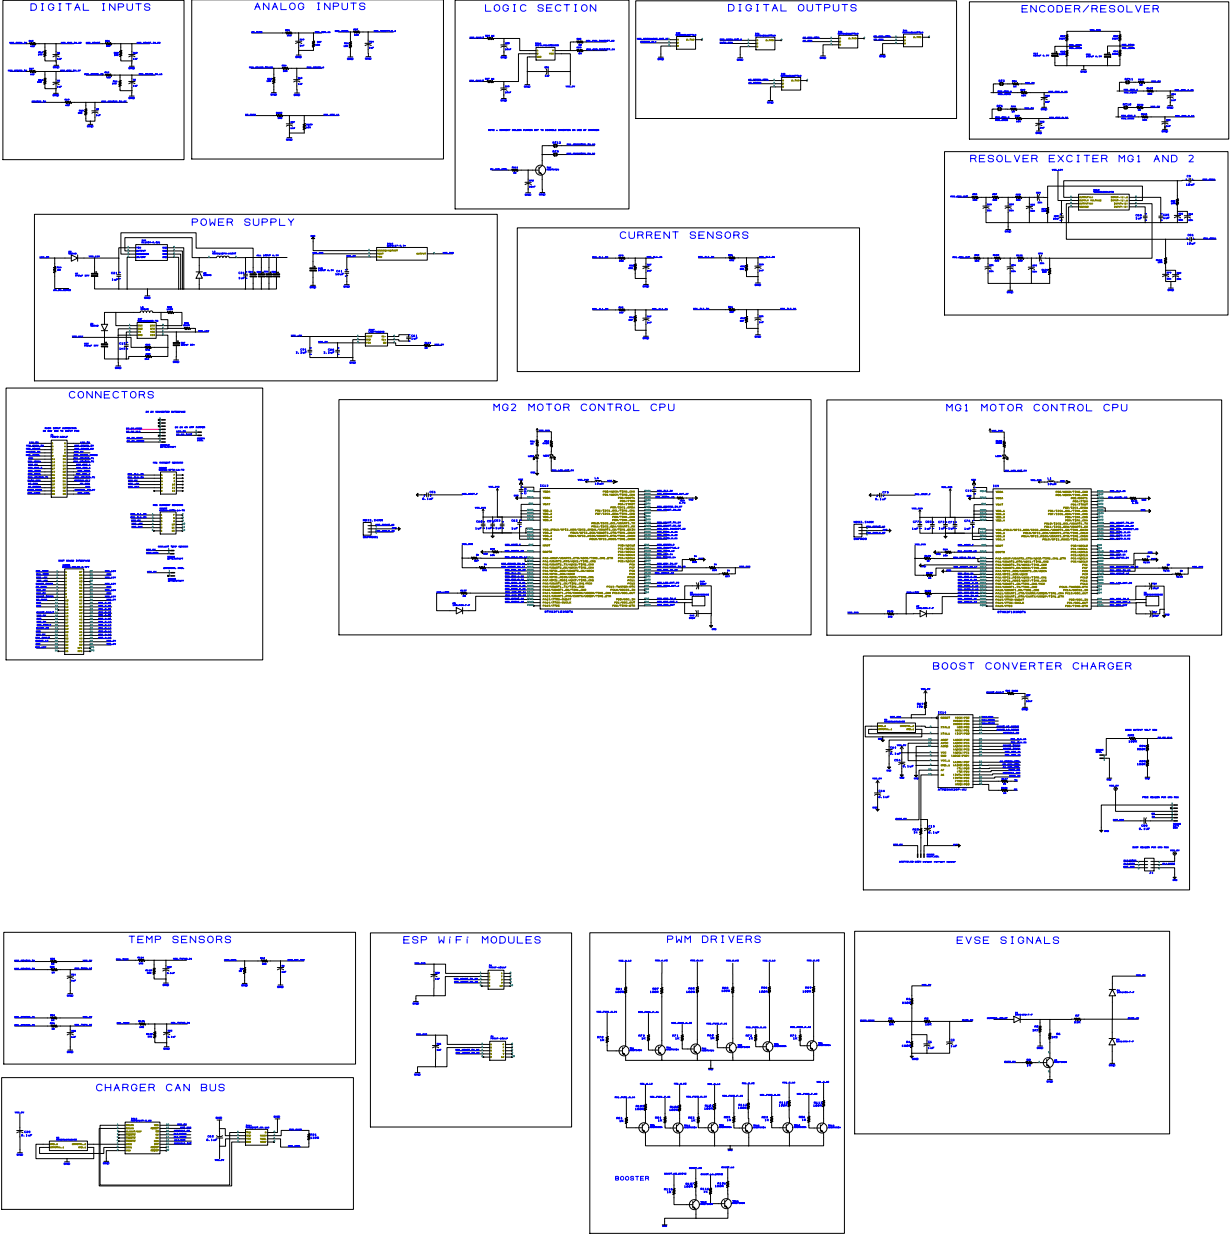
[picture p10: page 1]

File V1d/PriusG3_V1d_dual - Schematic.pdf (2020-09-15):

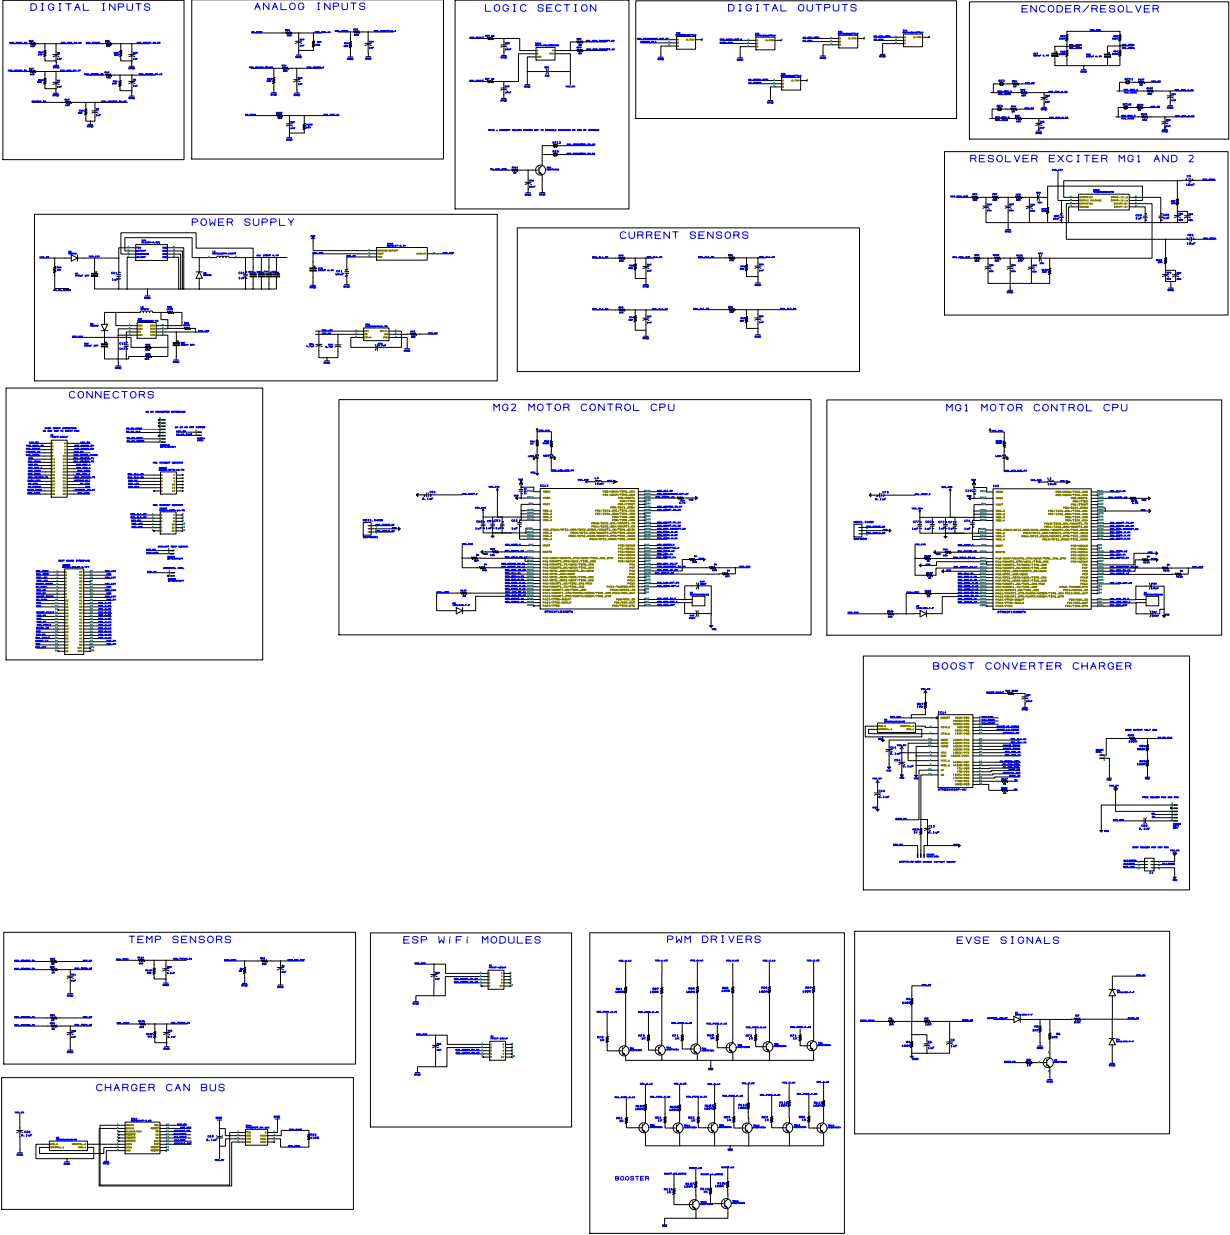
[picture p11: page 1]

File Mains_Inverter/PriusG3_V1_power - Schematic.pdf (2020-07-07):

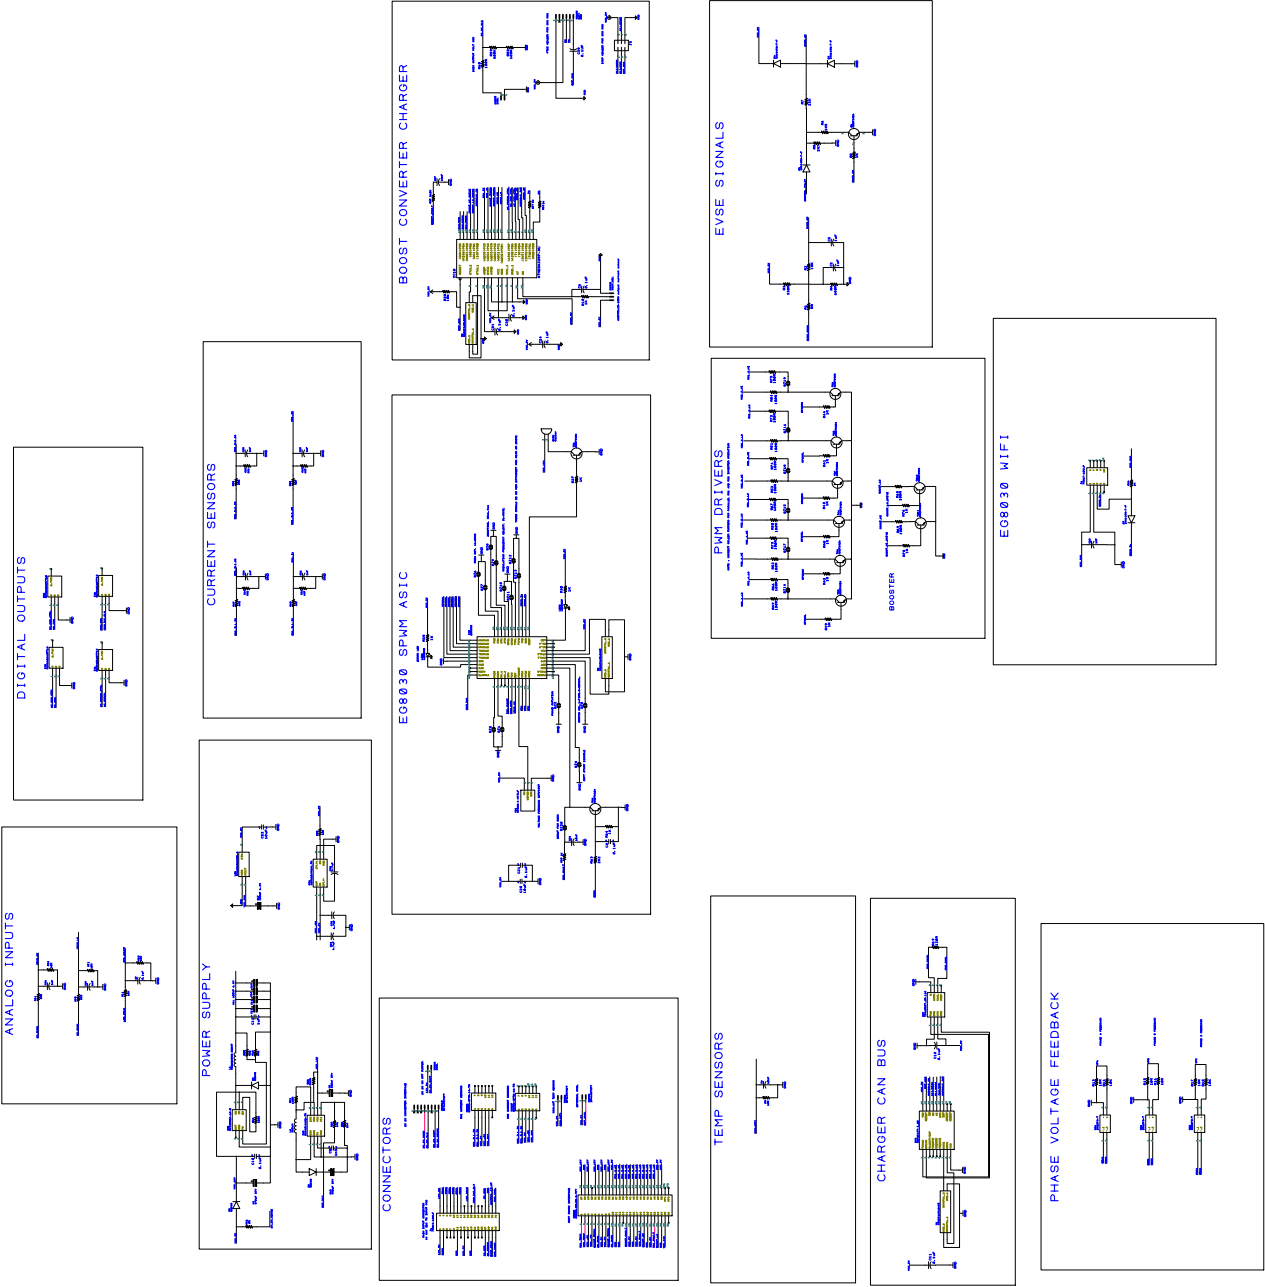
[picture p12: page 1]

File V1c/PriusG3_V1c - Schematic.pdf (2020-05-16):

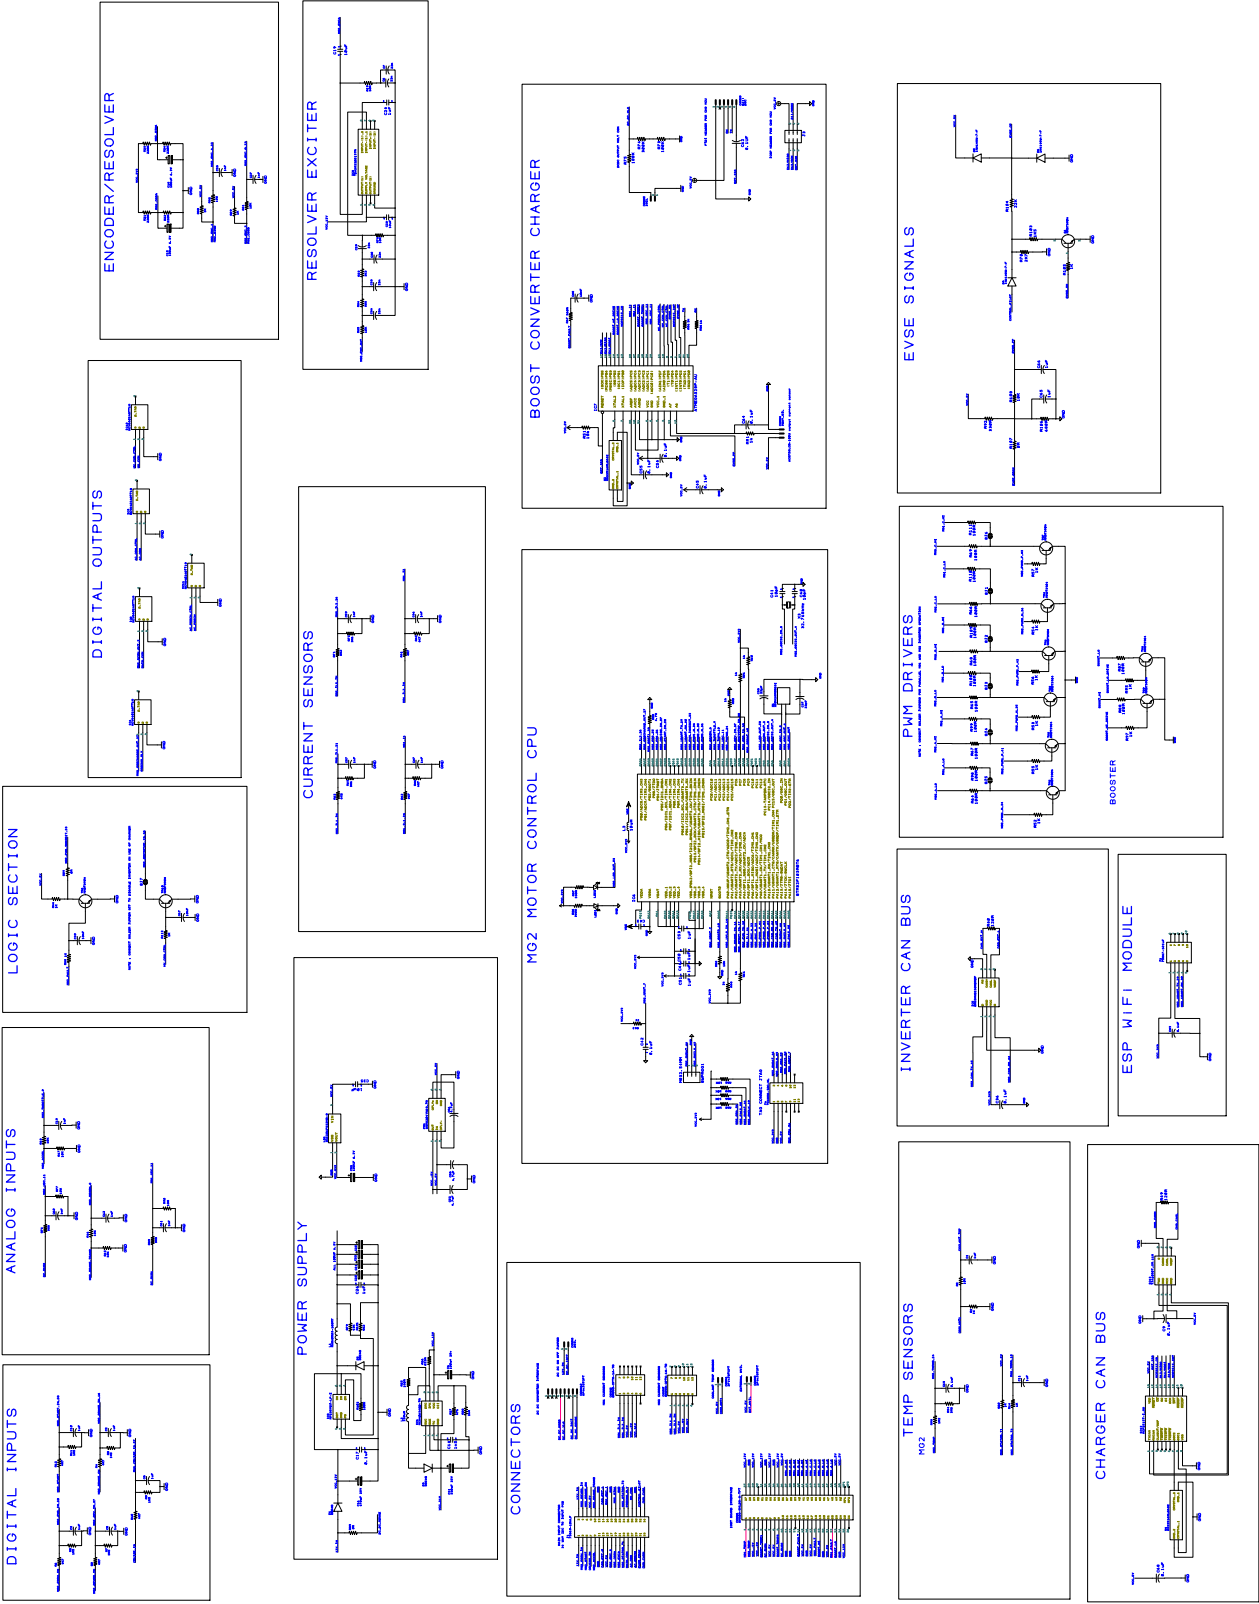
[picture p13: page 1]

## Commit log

2020-06-07 Add BOM CSV
    List of specialized parts that need to be acquired for hand placement.
    [PriusGen3HandPlacedParts.csv]
2021-01-18 Uploaded small board files.
    These are based on the V1d large board design but modified to match the outline and connector placement for inverters with the smaller 143mm board (Yaris/Auris/2012+Prius)
    Other modifications include moving the resistors that clash with the IDC, and adding a delay-on option for the DC-DC converter.
    [Toyota_G3_Small_dual_V1d.sch, Toyota_G3_Small_dual_V1d_BOM_JLC.xls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]
2022-01-22 Updated BOM file as JLC have changed the headings.
    Note I haven't checked the file contents still matches up.
    [Toyota_G3_Small_dual_V1d_BOM_JLC.xlsx]
2022-02-03 Add mains inverter design files
    [PriusG3_V1_power.sch, PriusG3_V1_power_BOM_JLC.xls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]
2025-09-05 Add Ampseal adapter board gerbers
2026-02-07 Add Transaxle Adapter plate drawings
    DXF and Freecad 1 source files for an adapter plate to fit the Gen3 P410 transaxle.
    [PriusGen3_Bell1-BodySketch.dxf, PriusGen3_Bell1.FCStd]
